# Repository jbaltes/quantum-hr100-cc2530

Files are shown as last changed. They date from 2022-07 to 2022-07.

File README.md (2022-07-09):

# About

quantum-hr100-cc2530 - fan controller board with mains power and zigbee

quantum-hr100-cc2530 is a open source hardware board.
It can controls pendulum fan Quantum HR 100 over zigbee.

# Warning

This project uses dangerous mains voltage. Be carefull.

## Structure

 * Terminal blocks for input power, fan supply and pwm signal
 * non isolated ACDC power supply
 * cc2530 rf-module
 * switchable fan supply with triac
 * cc2530 programming connector
 * i2c connector for e.g. temperature/humidity sensor

## Quantum HR 100

The pendulum fan Quantum HR 100 from aerauliqa has a two direction fan motor with pwm control unit.

The original pwm control works with 10Hz. A duty cycle of 50% stops the motor from running.
Maximum tested pwm frequency with 50% duty cylce to stop the motor was 400Hz.

The pwm input circuit of the motor clamps the voltage to 2.65V with about 5mA current at 3.3V supply voltage.

The pwm control voltage threshols are:
on-threshold: 2.0V
off-threshold: 1.0V

The pwm duty cycle thresholds are:
<= 43% on
>= 47% off
<= 53% off
>= 57% on

PWM frequency of 4Hz, 8Hz, 15Hz didn't work. 30Hz works fine.

## cc2530

CC2530 SZ1V5 module
30x20x4mm pitch 1.25mm

GND   1    24 RST#
GND   2    23 P0_0
3V3   3    22 P0_1
3V3   4    21 P0_2
P2_2  5    20 P0_3
P2_1  6    19 P0_4
P2_0  7    18 P0_5
P1_7  8    17 P0_6
P1_6  9    16 P0_7
P1_5 10    15 P1_0
P1_4 11    14 P1_1
P1_3 12    13 P1_2

A working configurable firmware for the zigbee module can be found at:
github.com/ptvoinfo/zigbee-configurable-firmware

## programming cc2530

### Raspberry Pi 1B

www.zigbee2mqtt.io/guide/adapters/flashing/alternative_flashing_methods.html

Rasphberry Pi need wiringPi (apt install wiringPi) - includes command gpio: "gpio readall" shows physical connector pins to wiring number mapping (wPi)

physical pin 13 -> wPi 2 (clock) -> DEBUG_CLK (DC) cc2530_P2_2
physical pin 15 -> wPi 3 (data) -> DEBUG_DATA (DD) cc2530_P2_1
physical pin 18 -> wPI 5 (reset) -> cc2530_RST#

 * read chip ID: cc_chipid -c 2 -d 3 -r 5
 * read firmware: cc_read -c 2 -d 3 -r 5
 * write firemware: cc_write -c 2 -d 3 -r 5 <firmware-hex-file>

### USB programmer

2x5 pin header assignment:
GND  1  2 VDD (3V3)
DC   3  4 DD
CS#  5  6 SCLK
RST# 7  8 MOSI
VDD  9 10 MISO

# License

The hardware is licensed under CERN OHL v.1.2. See COPYING.hardware for the complete license.

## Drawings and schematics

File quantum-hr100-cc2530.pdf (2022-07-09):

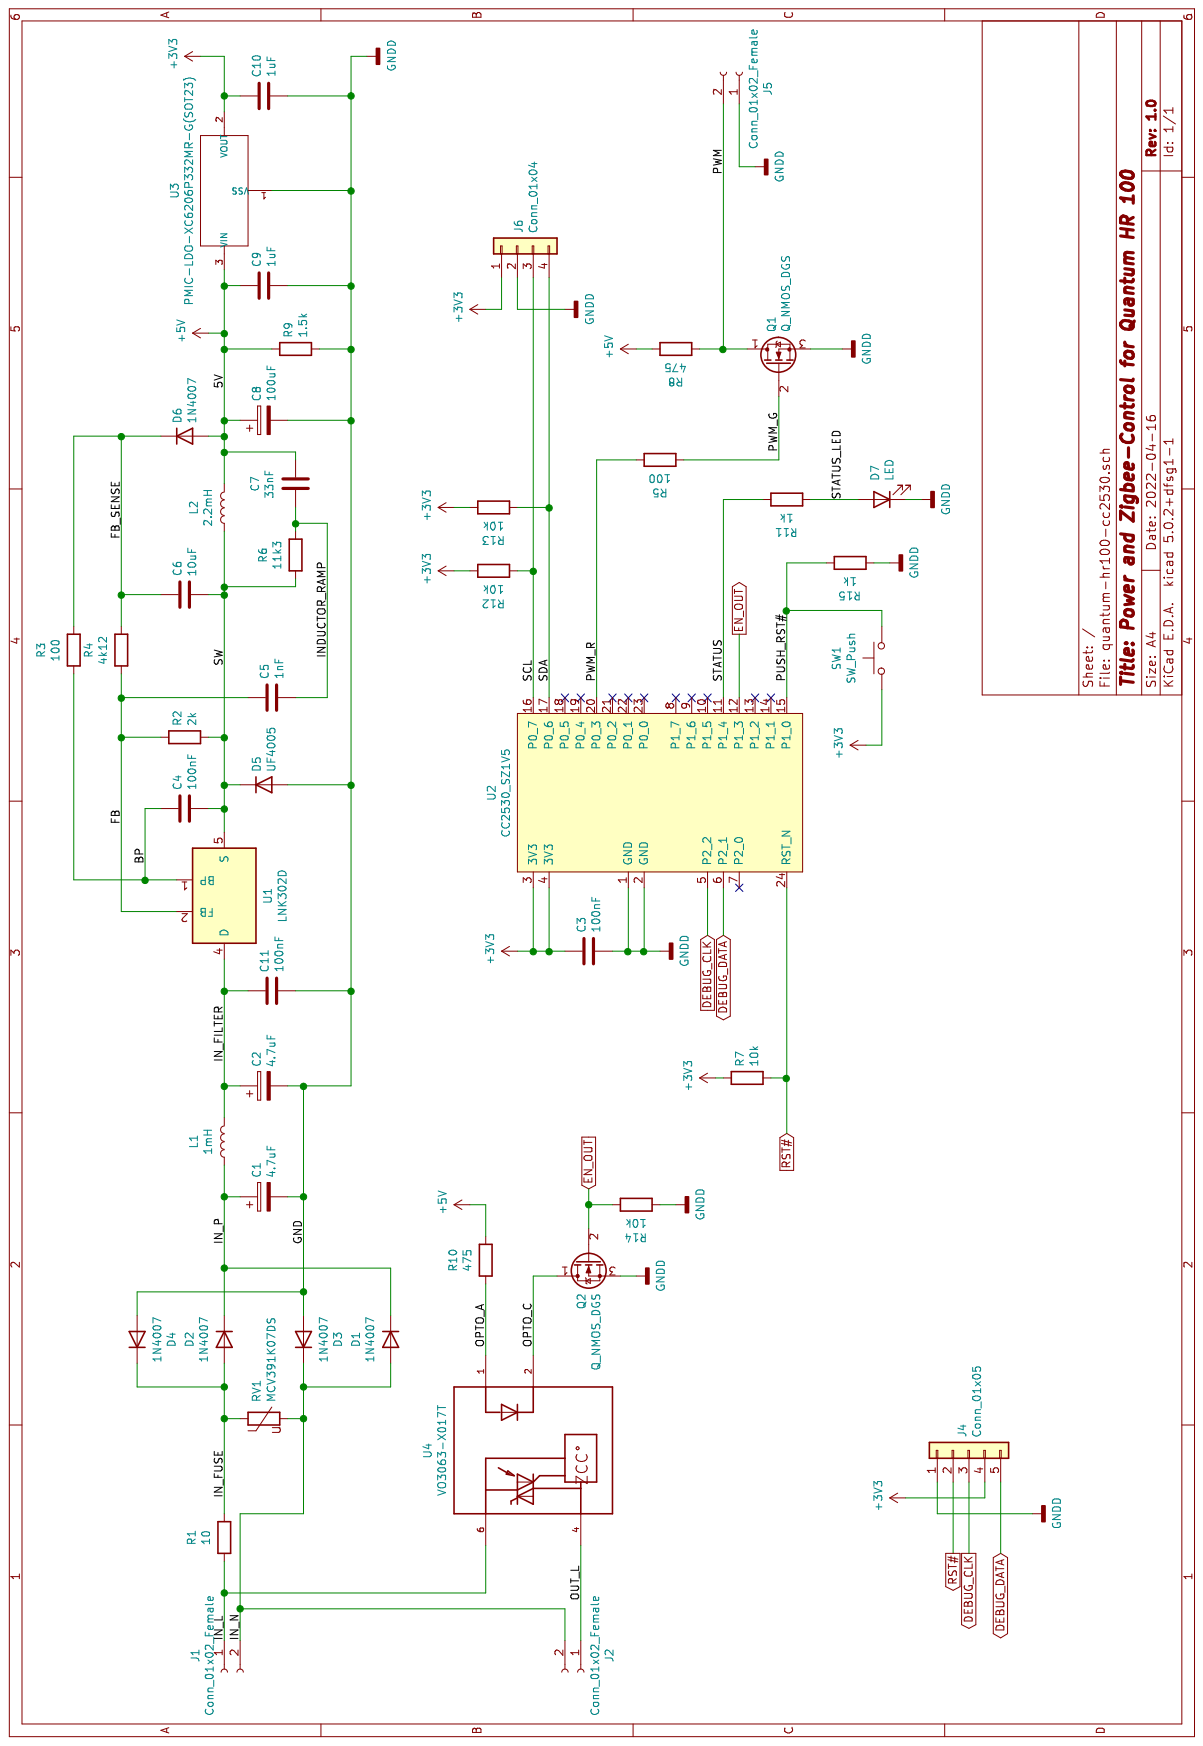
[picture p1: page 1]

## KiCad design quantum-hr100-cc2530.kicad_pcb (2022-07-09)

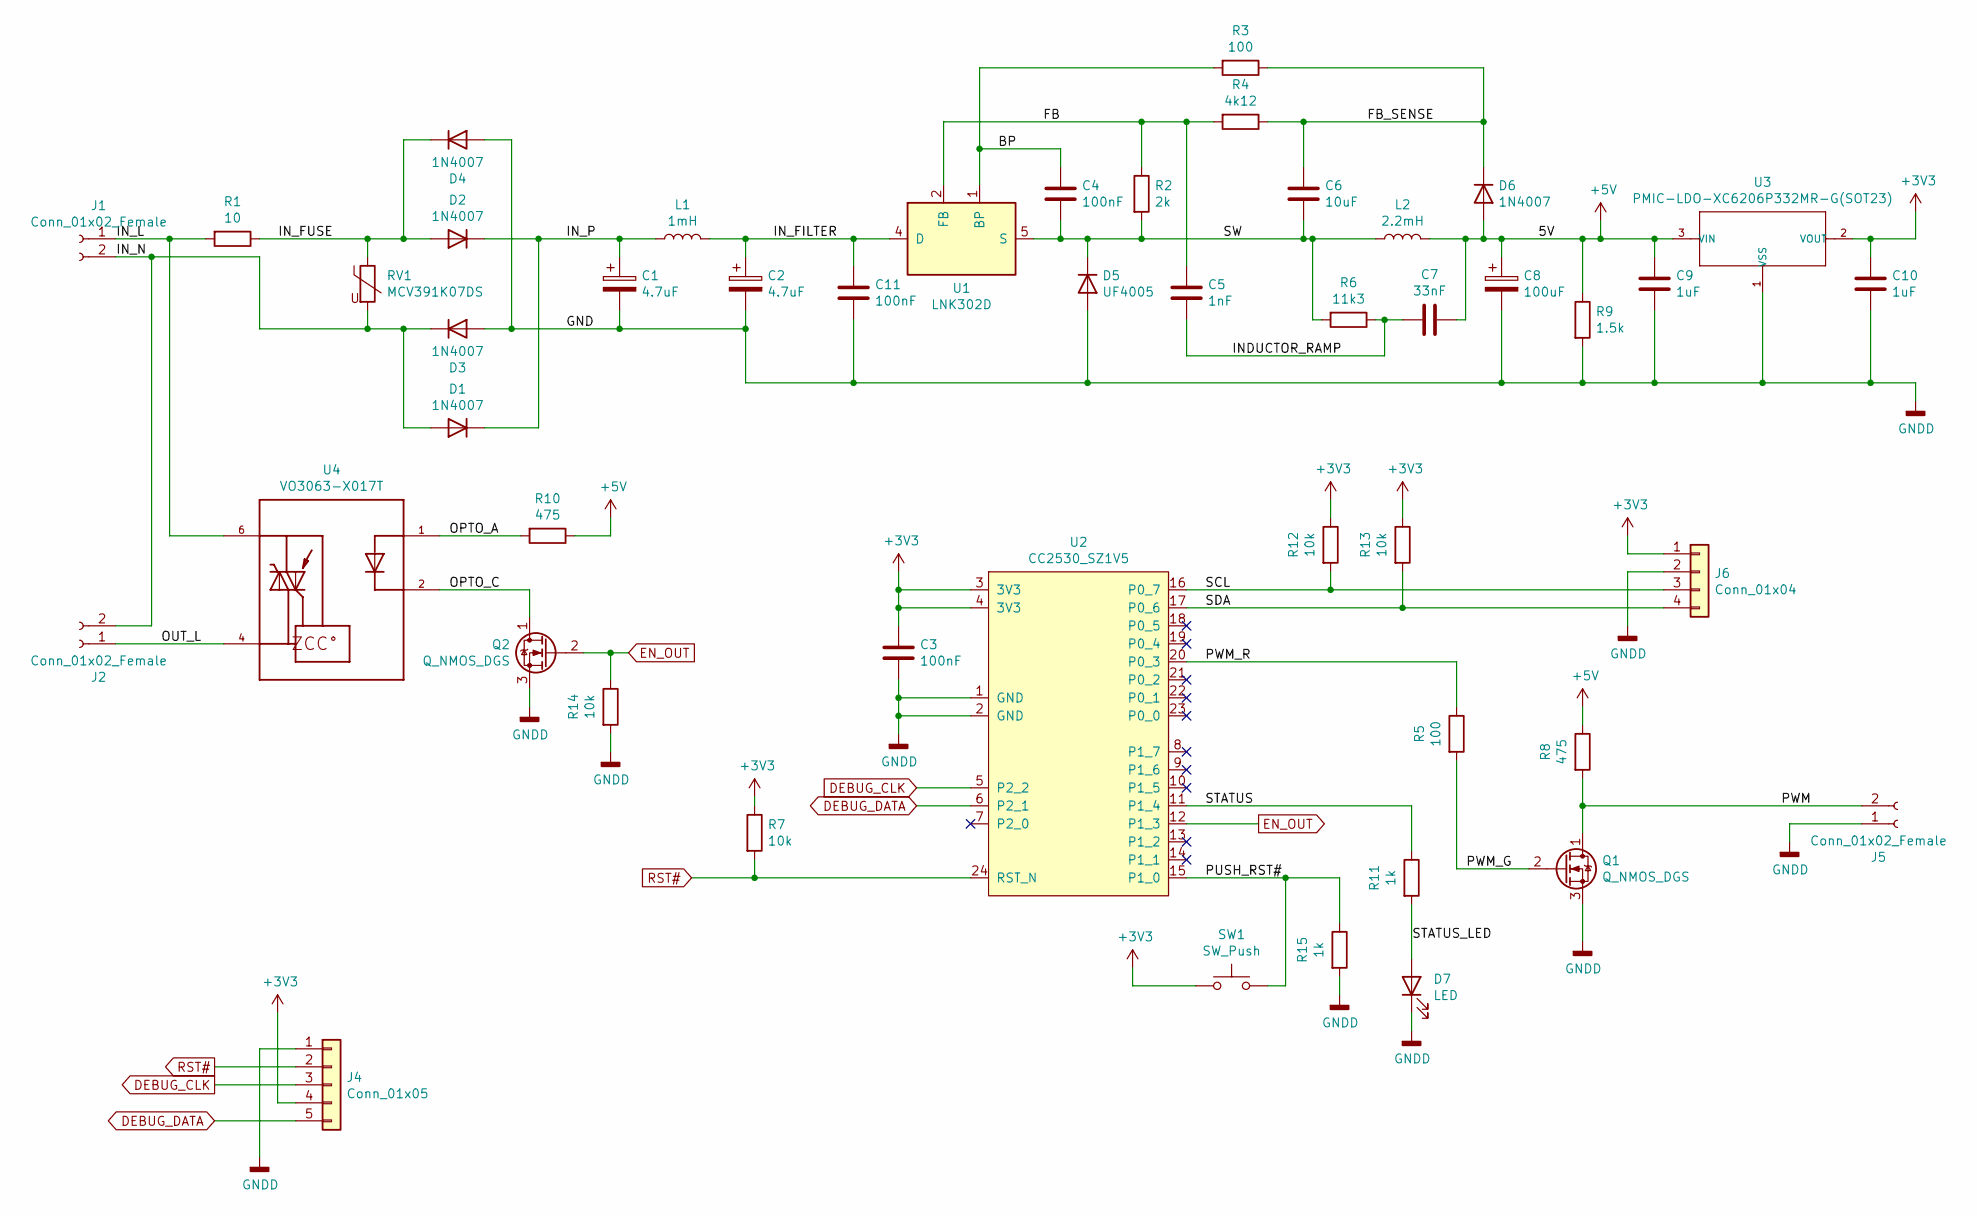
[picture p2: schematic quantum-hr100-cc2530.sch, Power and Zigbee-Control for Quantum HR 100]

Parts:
C1, C2: 4.7uF; CP_Radial_D10.0mm_P5.00mm
C3: 100nF; C_0603_1608Metric
C4: 100nF; C_1206_3216Metric_Pad1.33x1.80mm_HandSolder
C5: 1nF; C_0603_1608Metric_Pad1.05x0.95mm_HandSolder
C6: 10uF; C_1206_3216Metric_Pad1.33x1.80mm_HandSolder
C7: 33nF; C_0603_1608Metric_Pad1.05x0.95mm_HandSolder
C8: 100uF; CP_Radial_D5.0mm_P2.00mm
C9, C10: 1uF; C_0603_1608Metric
C11: 100nF; C_1210_3225Metric_Pad1.33x2.70mm_HandSolder
D1, D2, D3, D4, D6: 1N4007; D_SMA
D5: UF4005; D_SMA
D7: LED; LED_0603_1608Metric_Pad1.05x0.95mm_HandSolder
J1, J2, J5: Conn_01x02_Female; P-250-202
J4: Conn_01x05; PinHeader_1x05_P1.27mm_Vertical
J6: Conn_01x04; Molex_PicoBlade_53047-0410_1x04_P1.25mm_Vertical
L1: 1mH; L_Axial_L11.0mm_D4.5mm_P5.08mm_Vertical_Fastron_MECC
L2: 2.2mH; L_Radial_D9.5mm_P5.00mm_Fastron_07HVP
Q1, Q2: Q_NMOS_DGS; SOT-23
R1: 10; R_Axial_DIN0414_L11.9mm_D4.5mm_P5.08mm_Vertical
R2: 2k; R_1206_3216Metric_Pad1.30x1.75mm_HandSolder
R3: 100; R_0603_1608Metric_Pad1.05x0.95mm_HandSolder
R4: 4k12; R_0603_1608Metric_Pad1.05x0.95mm_HandSolder
R5: 100; R_1206_3216Metric_Pad1.30x1.75mm_HandSolder
R6: 11k3; R_1206_3216Metric_Pad1.30x1.75mm_HandSolder
R7: 10k; R_0603_1608Metric_Pad1.05x0.95mm_HandSolder
R8, R10: 475; R_0603_1608Metric_Pad0.98x0.95mm_HandSolder
R9: 1.5k; R_0603_1608Metric_Pad0.98x0.95mm_HandSolder
R11, R15: 1k; R_0603_1608Metric_Pad0.98x0.95mm_HandSolder
R12, R13, R14: 10k; R_0603_1608Metric_Pad0.98x0.95mm_HandSolder
RV1: MCV391K07DS; RV_Disc_D9mm_W5.7mm_P5mm
SW1: SW_Push; SW_PUSH_6mm_H13mm
U1: LNK302D; PowerIntegrations_SMD-8B
U2: CC2530_SZ1V5; CC2530_SZ1V5_HOLES
U3: PMIC-LDO-XC6206P332MR-G(SOT23); SOT-23; MPN XC6206P332MR-G
U4: VO3063-X017T; SOIC254P1030X460-6N

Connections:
+3V3: C3.1, C10.1, J4.4, J6.1, R7.1, R12.1, R13.1, SW1.1, U2.3 (3V3), U2.4 (3V3), U3.2 (VOUT)
+5V: C7.2, C8.1, C9.1, D6.2 (A), L2.2, R8.1, R9.1, R10.1, U3.3 (VIN)
/BP: C4.1, R3.2, U1.1 (BP)
/FB: C5.1, R2.1, R4.2, U1.2 (FB)
/FB_SENSE: C6.1, D6.1 (K), R3.1, R4.1
/INDUCTOR_RAMP: C5.2, C7.1, R6.1
/IN_FILTER: C2.1, C11.1, L1.2, U1.4 (D)
/IN_FUSE: D2.2 (A), D4.1 (K), R1.1, RV1.1
/IN_L: J1.1, R1.2, U4.6
/IN_N: D1.2 (A), D3.1 (K), J1.2, J2.2, RV1.2
/IN_P: C1.1, D1.1 (K), D2.1 (K), L1.1
/OPTO_A: R10.2, U4.1
/OPTO_C: Q2.1 (D), U4.2
/OUT_L: J2.1, U4.4
/PUSH_RST#: R15.1, SW1.2, U2.15 (P1_0)
/PWM: J5.2, Q1.1 (D), R8.2
/PWM_G: Q1.2 (G), R5.2
/PWM_R: R5.1, U2.20 (P0_3)
/SCL: J6.3, R12.2, U2.16 (P0_7)
/SDA: J6.4, R13.2, U2.17 (P0_6)
/STATUS: R11.1, U2.11 (P1_4)
/STATUS_LED: D7.2 (A), R11.2
/SW: C4.2, C6.2, D5.1 (K), L2.1, R2.2, R6.2, U1.5 (S), U1.6 (S), U1.7 (S), U1.8 (S)
DEBUG_CLK: J4.3, U2.5 (P2_2)
DEBUG_DATA: J4.5, U2.6 (P2_1)
EN_OUT: Q2.2 (G), R14.1, U2.12 (P1_3)
GNDD: C1.2, C2.2, C3.2, C8.2, C9.2, C10.2, C11.2, D3.2 (A), D4.2 (A), D5.2 (A), D7.1 (K), J4.1, J5.1, J6.2, Q1.3 (S), Q2.3 (S), R9.2, R14.2, R15.2, U2.1 (GND), U2.2 (GND), U3.1 (VSS)
RST#: J4.2, R7.2, U2.24 (RST_N)

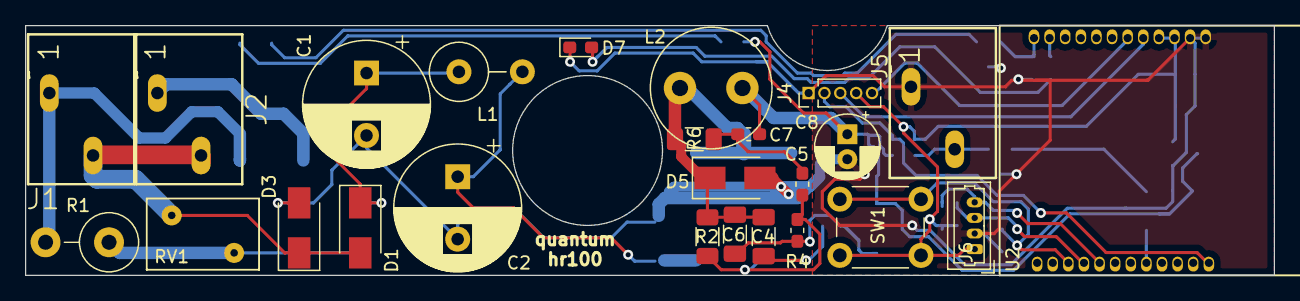
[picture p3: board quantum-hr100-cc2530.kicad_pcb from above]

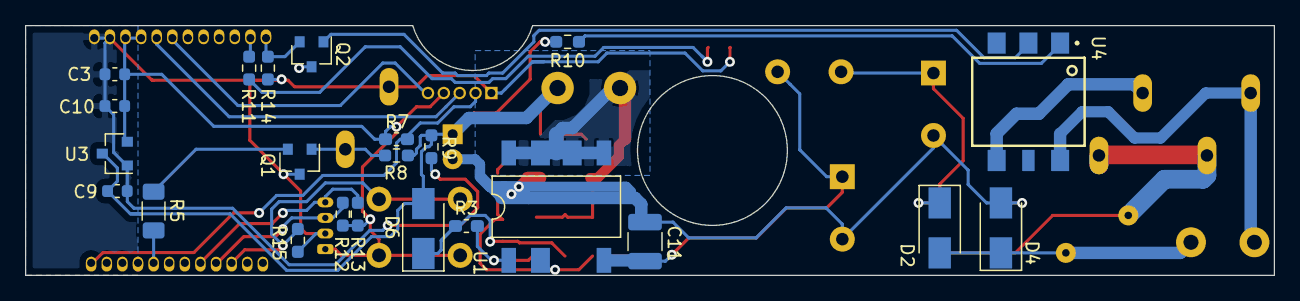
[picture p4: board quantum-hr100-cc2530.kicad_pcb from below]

Board: 2 copper layers, 100.0 x 20.0 mm, 48 parts (23 on the bottom side), 28 nets.
